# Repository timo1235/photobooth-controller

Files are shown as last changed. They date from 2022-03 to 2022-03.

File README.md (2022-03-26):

# Photobooth controller

This code is for controlling the shutter mechanism of a photobooth.
The whole documentation can be found at [https://blog.altholtmann.com/fotobox-selbstbau/](https://blog.altholtmann.com/fotobox-selbstbau/)

## Sketches
The two sketches under `photobooth - buzzer` and `photobooth - main` are projects for [PlatformIO and VSCode](https://platformio.org/install/ide?install=vscode).

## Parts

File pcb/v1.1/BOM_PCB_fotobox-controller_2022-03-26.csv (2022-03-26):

ID | Name | Designator | Footprint | Quantity | Manufacturer Part | Manufacturer | Supplier | Supplier Part | Price
1 | EL357N(B)(TA)-G | U1 | OPTO-SMD-4_L4.4-W4.1-P2.54-LS7.0-TL | 1 | EL357N(B)(TA)-G | EVERLIGHT | LCSC | C6649 | 0.069
2 | 100nF | C9,C1,C2,C3,C4,C5,C6,C7,C8,C10 | C0402_NEW | 10 | CL05B104KO5NNNC | SAMSUNG | LCSC | C1525 | 0.001
3 | 220Ω | R9,R1,R2,R3,R4,R5,R6,R7,R8,R10 | R0402 | 10 | 0402WGF2200TCE | UniOhm | LCSC | C25091 | 0.001
4 | WS2813B-B | LED9,LED1,LED2,LED3,LED4,LED5,LED6,LED7,LED8,LED10 | LED-SMD_6P-L5.0-W5.0-TL | 10 | WS2813B-B | Worldsemi | LCSC | C114592 | 0.134
5 | SS34_C8678 | D1 | DO-214AC_L4.3-W2.7-LS5.3-RD | 1 | SS34 | MDD | LCSC | C8678 | 0.043
6 | 330Ω | R11 | R0402 | 1 | 0402WGF3300TCE | UniOhm | LCSC | C25104 | 0.001
7 | 10uF | C11 | C0402 | 1 | CL05A106MQ5NUNC | SAMSUNG | LCSC | C15525 | 0.006
8 | KF128-2.54-4P | U4,U3,U2 | CONN-TH_4P-P2.54_KF128-2.54-4P | 3 | KF128-2.54-4P | Cixi Kefa Elec | LCSC | C474922 | 0.531
9 | 220S-1*7P H=8.5MM Ytype Gold-plated | DISPLAY | HDR-TH_7P-P2.54-V-F | 1 | 220S-1*7P H=8.5MM Ytype Gold-plated | Ckmtw | LCSC | C124418 | 0.173
10 | TS665CJ | SW1,SW2 | SW-TH_4P-L6.0-W6.0-P4.50-LS6.5 | 2 | TS665CJ | SHOU HAN | LCSC | C393938 | 0.012
11 | 2.54_1x15 | H1,H2 | HDR-TH_15P-P2.54-V-F | 2 | 220S-1*15P H=8.5MM Ytype Gold-plated | Ckmtw | LCSC | C124408 | 0.203

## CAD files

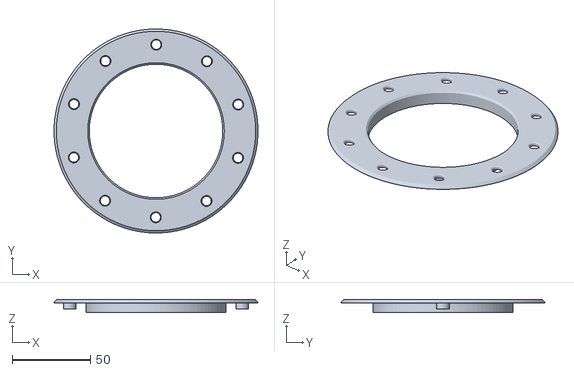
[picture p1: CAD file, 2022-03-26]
Blende um den ring - Fusion360/blende.stl
130.0 x 130.0 x 8.00

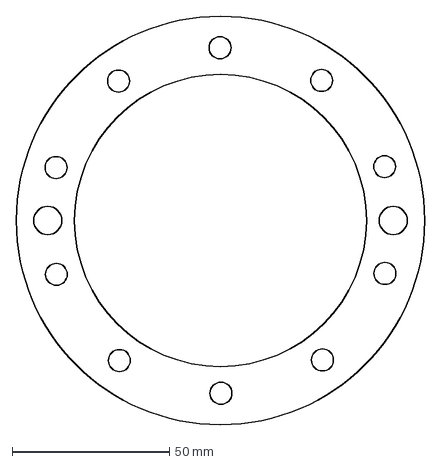
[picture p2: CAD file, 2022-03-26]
Blende um den ring - Fusion360/blende dxf fuer fraese.dxf
130.0 x 130.0 mm

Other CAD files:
Blende um den ring - Fusion360/fotobox controller.f3d

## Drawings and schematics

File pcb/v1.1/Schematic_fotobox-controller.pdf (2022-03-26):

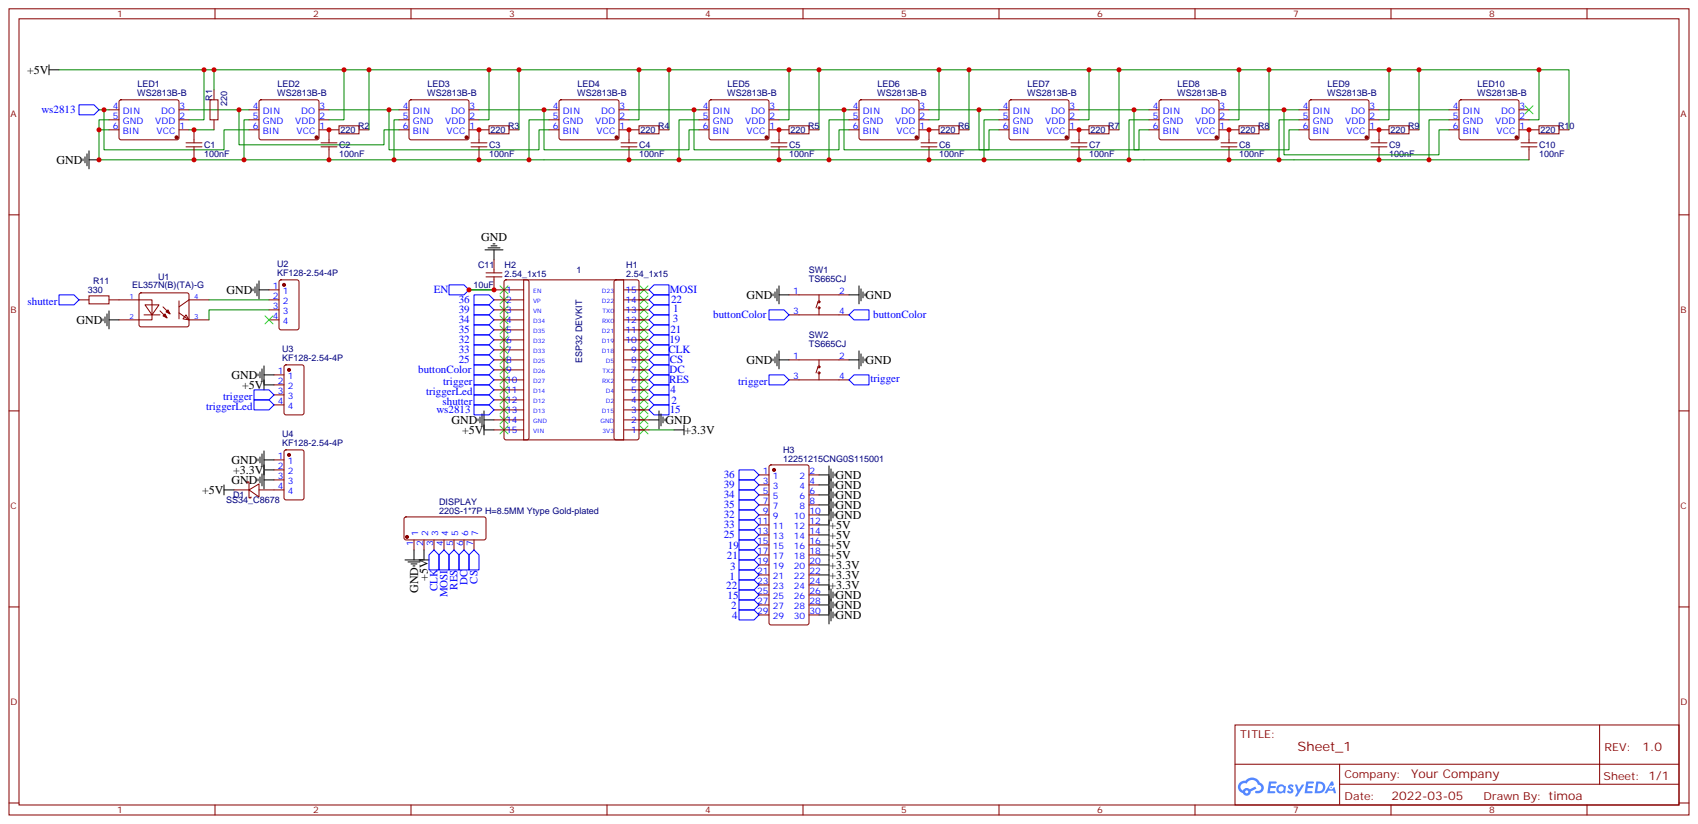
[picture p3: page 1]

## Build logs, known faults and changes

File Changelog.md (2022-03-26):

# Fotobox Controller

## Changelog
### v1.1
- Changed wrong label for trigger and color
- Changed R11 to be placed on the bottom side
- Changed C11 to be placed on the bottom side

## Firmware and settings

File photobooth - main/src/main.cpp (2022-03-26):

/**
 * Photobooth controller sketch v1.0
 * find out more: blog.altholtmann.com
 * by Timo Altholtmann
 * 
 * ***********************    General Notes    *****************************
 * - Uncomment means removing the 2 // in front of #define.
 * 
 **/
#include <Arduino.h>
// Debugging. If enabled, the sketch will print DEBUGGING states to the serial monitor
// with 115200 Baudrate
// Default: commented
#define DEBUG // Uncomment to output DEBUGGING messages

// Mac-Adress of the photobooth controller. This is the most important part and has to match the defined Mac-Adress in the 
// photobooth buzzer sketch otherwise a communication is not possible. Only needs to be changed, if there are other 
// photobooth controller in range.
// Every number can be changed to a value between 0-9. For example {0, 5, 0, 9, 0, 1}. That should be enough possible
// combinations to find a unique one
// Default: { 0x5, 0x0, 0x0, 0x0, 0x0, 0x1 }
#define BOOTH_MAC_ADDRESS { 0x5E, 0x0, 0x0, 0x0, 0x0, 0x1 }

// Should it be possible to abort the sequence with another button press
#define ABORT_ACTIVE true

// --------------------------------------------------------------------------------------------------------------------
// END Configuration - No need to change anything below - unless you know what you are doing!!
// --------------------------------------------------------------------------------------------------------------------

// Includes
#include <WiFi.h>
#include <esp_wifi.h>
#include <esp_now.h>
#include <EEPROM.h>
// WS2812 library
#include <Adafruit_NeoPixel.h>
// Display library
#include <U8x8lib.h>
// Debouncing library
#include <Bounce2.h>

enum COMMANDS 
{
    BUTTON_TRIGGERED,
    RESET_TRIGGERED,
};

typedef struct DATA_TO_BOOTH
{
    COMMANDS command;
    uint16_t payload;
} DATA_TO_BOOTH;

uint8_t newMACAddress[] = BOOTH_MAC_ADDRESS;

// Struct for incoming data
DATA_TO_BOOTH dataToBooth;

const byte colorSwitchPin = 26;
const byte triggerPin = 27;
const byte triggerLedPin = 14;
const byte shutterPin = 12;
const byte ws2813Pin = 13;
const byte ws2813LedCount = 10; 
byte ledClockBrightness = 50;
Adafruit_NeoPixel ledClock = Adafruit_NeoPixel(ws2813LedCount, ws2813Pin, NEO_GRB + NEO_KHZ800);
TaskHandle_t SecondCore;
U8X8_SSD1306_128X64_NONAME_4W_HW_SPI u8x8(/* cs=*/5, /* dc=*/ 17, /* reset=*/ 16);
Bounce buttonTrigger = Bounce();
Bounce buttonColor = Bounce();

struct RGB {
  char color[15];
  uint32_t colorCode;
};

RGB colors[] = {
  {"Aus", ledClock.Color(1,1,1)},
  {"Weiss", ledClock.Color(255,255,255)},
  {"Rot", ledClock.Color(255,0,0)},
  {"Gruen", ledClock.Color(0,255,0)},
  {"Blau", ledClock.Color(0,0,255)},
  {"Pink", ledClock.Color(253,35,253)},
  {"Gelb", ledClock.Color(248,255,27)}
};

uint8_t sequenceTimes[] = { 0, 2, 4, 6, 8, 10, 12 };

uint8_t currentClockColor;
bool shouldStartSequence = false;
uint32_t sequenceStartTime_MS = 0;
bool shouldAbortSequence = false;
uint32_t colorSwitchButtonLastPressed_MS = millis();
uint8_t currentSequenceTime;

#ifdef DEBUG    //Macros are usually in all capital letters.
#define DPRINT(...)    Serial.print(__VA_ARGS__)     //DPRINT is a macro, debug print
#define DPRINTLN(...)  Serial.println(__VA_ARGS__)   //DPRINTLN is a macro, debug print with new line
#else
#define DPRINT(...)     //now defines a blank line
#define DPRINTLN(...)   //now defines a blank line
#endif

void SecondCoreCode(void *pvParameters);

bool shouldAbort() {
  if(shouldAbortSequence) {
    DPRINTLN("shouldAbort: Indicate abort sequence with red blinks");
    for (uint8_t i = 0; i < 2; i++) {
      ledClock.fill(colors[2].colorCode,0,ws2813LedCount);
      ledClock.show();
      digitalWrite(triggerLedPin, LOW);
      delay(200);
      ledClock.fill(colors[0].colorCode,0,ws2813LedCount);
      ledClock.show();
      digitalWrite(triggerLedPin, HIGH);
      delay(200);
    }
    shouldStartSequence = false;
    shouldAbortSequence = false;
    sequenceStartTime_MS = 0;
    return true;
  }

  return false;
}

void takePicture() {
  DPRINTLN("Taking a picture!");
  digitalWrite(shutterPin, HIGH);
  delay(100);
  digitalWrite(shutterPin, LOW);
}

void ledSequence(int waitTime)
{
  DPRINT("ledSequence: Start - waitTime: ");
  DPRINTLN(waitTime);
  // blink leds if there is enough time
  if (waitTime > 1000) {
    DPRINTLN("ledSequence: Blink Leds before the sequence");
    for (uint8_t i = 0; i < 3; i++) {
      ledClock.fill(colors[currentClockColor].colorCode,0,ws2813LedCount);
      ledClock.show();
      digitalWrite(triggerLedPin, LOW);
      delay(100);
      ledClock.fill(colors[0].colorCode,0,ws2813LedCount);
      ledClock.show();
      digitalWrite(triggerLedPin, HIGH);
      delay(100);
      waitTime -= 100 * 2;
    }
  }
  // start the actual led sequence
  DPRINTLN("ledSequence: Led ring sequence start");
  uint16_t waitTimeStep = waitTime / ws2813LedCount;
  for (int i = ws2813LedCount-1; i >= 0; i--) {
    // Check if the sequence should be aborted
    if(shouldAbort() && ABORT_ACTIVE) return;
    ledClock.setPixelColor(i, colors[currentClockColor].colorCode);
    ledClock.show();
    // dont wait when the last led turns on - so the picture is taken faster
    if (i != 0) {
      delay(waitTimeStep);
    }
  }
  ledClock.fill(colors[1].colorCode,0,ws2813LedCount);
  ledClock.show();
  takePicture();
  delay(1000);
  ledClock.fill(colors[0].colorCode,0,ws2813LedCount);
  ledClock.show();
}

char *getMacStrFromAddress(uint8_t *address)
{
  static char macStr[18];
  // Copies the sender mac address to a string
  snprintf(macStr, sizeof(macStr), "%02x:%02x:%02x:%02x:%02x:%02x", address[0], address[1], address[2], address[3], address[4], address[5]);
  return macStr;
}

void processButtonTriggered() {
  // Abort when sequence has already startet. But only if some time went by to prevent fast double clicks
  if(!shouldAbortSequence && sequenceStartTime_MS != 0 && (millis() - sequenceStartTime_MS) > 1000) {
    DPRINTLN("OnDataRecv: Should abort sequence");
    shouldAbortSequence = true;
  } else if (sequenceStartTime_MS == 0 && !shouldStartSequence && !shouldAbortSequence) {
    DPRINTLN("OnDataRecv: Should start the sequence");
    shouldStartSequence = true;
  }
}

// callback function that will be executed when data is received
void OnDataRecv(const uint8_t *address, const uint8_t *incomingData, int len)
{
  DPRINTLN("OnDataRecv: Got Message");
  memcpy(&dataToBooth, incomingData, sizeof(dataToBooth));
  if(dataToBooth.command == COMMANDS::BUTTON_TRIGGERED) {
    processButtonTriggered();
  }
}

void setUpWifi()
{
  WiFi.enableLongRange(true);
  WiFi.mode(WIFI_STA);

  DPRINT("My old Mac Address: ");
  DPRINTLN(WiFi.macAddress());

  esp_wifi_set_ps(WIFI_PS_NONE);
  esp_wifi_set_mac(WIFI_IF_STA, &newMACAddress[0]);

  DPRINT("My new Mac Address: ");
  DPRINTLN(WiFi.macAddress());

    if (esp_now_init() != ESP_OK)
    {
      DPRINTLN("Error initializing ESP-NOW. Things wont work");
      return;
    }

    esp_now_register_recv_cb(OnDataRecv);
}

void updateDisplay() {
  u8x8.setFont(u8x8_font_profont29_2x3_f);
  u8x8.clearDisplay();
  u8x8.drawString(0,0,colors[currentClockColor].color);
  u8x8.setCursor(0,5);
  u8x8.print(sequenceTimes[currentSequenceTime]);
  u8x8.print(" Sec.");

}

void setup() {
#ifdef DEBUG
  Serial.begin(115200);
#endif
  EEPROM.begin(2);

  currentClockColor = EEPROM.read(0);
  // Fallback
  if(currentClockColor < 0 || currentClockColor > sizeof(colors) / sizeof(RGB)) currentClockColor = 4;
  currentSequenceTime = EEPROM.read(1);
  // Fallback
  if(currentSequenceTime < 0 || currentSequenceTime > sizeof(sequenceTimes) / sizeof(uint8_t)) currentSequenceTime = 3;

  buttonTrigger.attach(triggerPin, INPUT_PULLUP);
  buttonTrigger.interval(5); // interval in ms
  buttonColor.attach(colorSwitchPin, INPUT_PULLUP);
  buttonColor.interval(5); // interval in ms

  pinMode(shutterPin, OUTPUT);
  digitalWrite(shutterPin, LOW);
  pinMode(triggerLedPin, OUTPUT);
  digitalWrite(triggerLedPin, HIGH);

  ledClock.begin();
  ledClock.setBrightness(ledClockBrightness);
  ledClock.fill(colors[0].colorCode,0,ws2813LedCount);
  ledClock.show();

  setUpWifi();

  u8x8.begin();
  u8x8.setFlipMode(1);
  updateDisplay();

  // Setup dual core
  xTaskCreatePinnedToCore(
    SecondCoreCode, /* Task function. */
    "SecondCore",   /* name of task. */
    10000,           /* Stack size of task */
    NULL,            /* parameter of the task */
    1,               /* priority of the task */
    &SecondCore,    /* Task handle to keep track of created task */
    0);

  DPRINTLN("setup: done!");
}

void loop() {
  buttonTrigger.update();
  buttonColor.update();

  // ********************
  // buttonTrigger
  // ********************
  // Short press handling
  if (buttonTrigger.rose())
  {
    processButtonTriggered();
  }

  // ********************
  // buttonColor
  // ********************
  // Short press handling
  if (buttonColor.rose())
  {
      if (buttonColor.previousDuration() < 1000)
      {
        currentClockColor++;
        if(currentClockColor == sizeof(colors) / sizeof(RGB)) currentClockColor = 1;
        updateDisplay();
        EEPROM.write(0, currentClockColor);
        EEPROM.commit();
      } 
  }
  // long press handling - reset postion
  if (buttonColor.read() == LOW)
  {
    if (buttonColor.currentDuration() > 1000)
    {
      while(buttonColor.read() == LOW) {
        currentSequenceTime++;
        if(currentSequenceTime == sizeof(sequenceTimes) / sizeof(uint8_t)) currentSequenceTime = 0;
        updateDisplay();
        for (int i = 0; i < 100; i++)
        {
          buttonColor.update();
          delay(10);
        }
      }
      EEPROM.write(1, currentSequenceTime);
      EEPROM.commit();
    }
  }

  delay(1);
}

void SecondCoreCode(void *pvParameters)
{
  // displayInit();

  for (;;)
  {
    // updateDisplay();
    if(shouldStartSequence) {
      shouldStartSequence = false;
      sequenceStartTime_MS = millis();
      ledSequence(sequenceTimes[currentSequenceTime] * 1000);
      shouldStartSequence = false;
      sequenceStartTime_MS = 0;
      shouldAbortSequence = false;
    }
    vTaskDelay(1);
  }
}

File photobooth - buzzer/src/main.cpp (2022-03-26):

/**
 * Photobooth Buzzer Sketch v1.0
 * find out more: blog.altholtmann.com
 * by Timo Altholtmann
 * 
 * ***********************    General Notes    *****************************
 * - Uncomment means removing the 2 // in front of #define.
 * 
 **/
#include <Arduino.h>
// Debugging. If enabled, the sketch will print DEBUGGING states to the serial monitor
// with 115200 Baudrate
// Default: commented
#define DEBUG // Uncomment to output DEBUGGING messages

// Mac-Adress of the photobooth controller. This is the most important part and has to match the defined Mac-Adress in the 
// photobooth buzzer sketch otherwise a communication is not possible. Only needs to be changed, if there are other 
// photobooth controller in range.
// Default: { 0x5E, 0x0, 0x0, 0x0, 0x0, 0x1 }
#define BOOTH_MAC_ADDRESS { 0x5E, 0x0, 0x0, 0x0, 0x0, 0x1 }

// --------------------------------------------------------------------------------------------------------------------
// END Configuration - No need to change anything below - unless you know what you are doing!!
// --------------------------------------------------------------------------------------------------------------------
#ifdef ESP32
  #include <WiFi.h>
  #include <esp_wifi.h>
  #include <esp_now.h>
#else
  #include <ESP8266WiFi.h>
  #include <espnow.h>
#endif

#ifdef DEBUG    //Macros are usually in all capital letters.
#define DPRINT(...)    Serial.print(__VA_ARGS__)     //DPRINT is a macro, debug print
#define DPRINTLN(...)  Serial.println(__VA_ARGS__)   //DPRINTLN is a macro, debug print with new line
#else
#define DPRINT(...)     //now defines a blank line
#define DPRINTLN(...)   //now defines a blank line
#endif

enum COMMANDS 
{
    BUTTON_TRIGGERED,
    RESET_TRIGGERED,
};

typedef struct DATA_TO_BOOTH
{
    COMMANDS command;
    uint16_t payload;
} DATA_TO_BOOTH;

// Struct for outgoing data
DATA_TO_BOOTH dataToBooth = {COMMANDS::BUTTON_TRIGGERED,0};

// Programm vars
uint8_t boothMacAddress[] = BOOTH_MAC_ADDRESS;

#ifdef ESP32
    esp_now_peer_info_t peerInfo;
    RTC_DATA_ATTR uint16_t bootCount = 0;
#endif
// Interrupt pin
const gpio_num_t interruptPin = GPIO_NUM_25;

char *getMacStrFromAddress(uint8_t *address)
{
    static char macStr[18];
    // Copies the sender mac address to a string
    snprintf(macStr, sizeof(macStr), "%02x:%02x:%02x:%02x:%02x:%02x", address[0], address[1], address[2], address[3], address[4], address[5]);
    return macStr;
}

void goToSleep()
{
    DPRINTLN("Going to sleep now");
    #ifdef ESP32
        // Use external pin for wakeup
        esp_sleep_enable_ext0_wakeup(interruptPin, 0);
        esp_wifi_stop();
        // esp_sleep_enable_timer_wakeup(intveral_s * 1000000);
        esp_deep_sleep_start();
    #else
        ESP.deepSleep(0);
    #endif
}

void sendMessageToBooth()
{
    #ifdef ESP32
    // Send message via ESP-NOW
    esp_err_t result = esp_now_send(boothMacAddress, (uint8_t *)&dataToBooth, sizeof(dataToBooth));
    if (result != ESP_OK)
    {
        DPRINTLN("Error sending the data - Things wont work");
    }
    #else
        esp_now_send(boothMacAddress, (uint8_t *) &dataToBooth, sizeof(dataToBooth));
    #endif
}

void setupWifi()
{
  #ifdef ESP32
    WiFi.enableLongRange(true);
  #else 
    WiFi.disconnect();
    ESP.eraseConfig();
  #endif
    WiFi.mode(WIFI_STA);

  DPRINT("My Mac Address: ");
  DPRINTLN(WiFi.macAddress());

    //Init ESP-NOW
    if (esp_now_init() != 0)
    {
        DPRINTLN("Error initializing ESP-NOW. Things wont work");
        goToSleep();
        return;
    }
  
  #ifdef ESP32
    // Register mower esp32 as peer
    memcpy(peerInfo.peer_addr, boothMacAddress, 6);
    peerInfo.channel = 0;
    peerInfo.encrypt = false;
    // Add peer
    if (esp_now_add_peer(&peerInfo) != ESP_OK)
    {
        DPRINTLN("Failed to add peer. Things wont work");
        goToSleep();
    }
  #else 
    esp_now_set_self_role(ESP_NOW_ROLE_CONTROLLER);
    esp_now_add_peer(boothMacAddress, ESP_NOW_ROLE_SLAVE, 1, NULL, 0);
  #endif
}

#ifdef ESP32
  void checkWakeUpReason()
  {
      esp_sleep_wakeup_cause_t wakeup_reason;
      wakeup_reason = esp_sleep_get_wakeup_cause();
      if (wakeup_reason == ESP_SLEEP_WAKEUP_EXT0)
      {
          DPRINTLN("Wake up by interrupt");
          dataToBooth.command = COMMANDS::BUTTON_TRIGGERED;
          sendMessageToBooth();
      }
  }
#endif

void setup()
{
  #ifdef DEBUG
    Serial.begin(115200);
  #endif

  setupWifi();
  pinMode(LED_BUILTIN, OUTPUT);
  digitalWrite(LED_BUILTIN, HIGH);

  #ifdef ESP32
    esp_deep_sleep_disable_rom_logging();
    bootCount++;
    DPRINT("BootCount: ");
    DPRINTLN(bootCount);

    pinMode(interruptPin, INPUT_PULLUP);
    checkWakeUpReason();
  #endif
}

void loop() {
    #ifndef ESP32
      sendMessageToBooth();
    #endif

    delay(10);

    goToSleep();
}

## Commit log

2022-03-26 Added some files
    [Battery Calculation.xlsx, blende dxf fuer fraese.dxf, blende.stl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]
2023-06-29 Use older framework package to prevent boot loop
2023-10-16 Fix arduino framework version
